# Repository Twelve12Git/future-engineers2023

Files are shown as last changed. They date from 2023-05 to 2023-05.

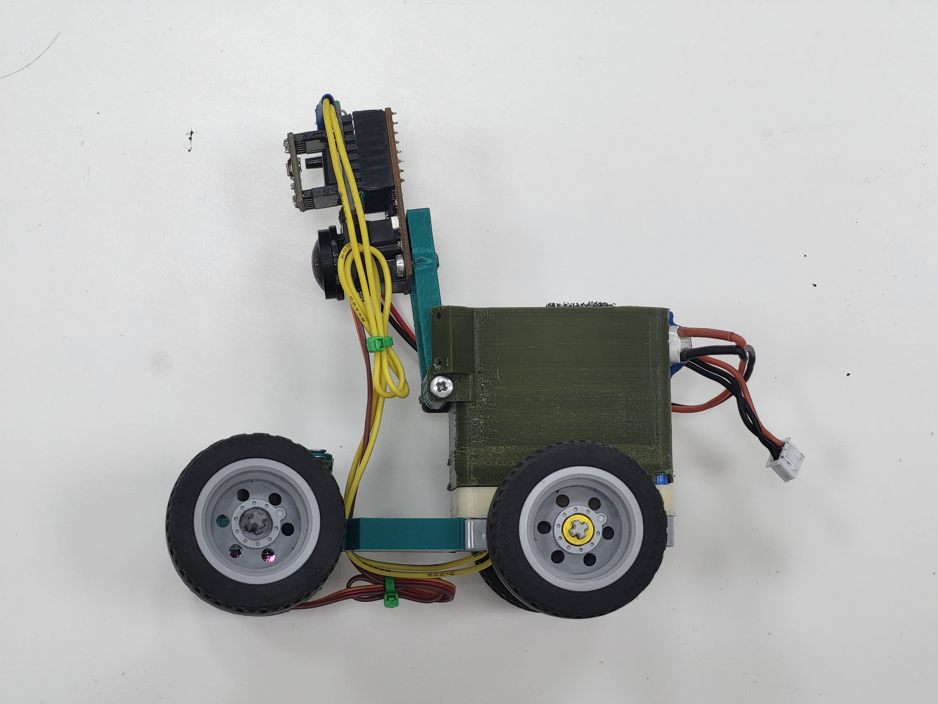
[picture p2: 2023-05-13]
v-photos/слева.jpg

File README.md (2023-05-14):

Во время реализации системы перемещения или же робота, в приоритет ставилась в первую очередь простота сборки и взаимозаменяемость деталей в случае поломки или необходимости внести коррективы в конструкцию. Во время первичного обсуждения конструкции было принято решение использовать О-образную деталь LEGO как основу корпуса, из этого последовало логичное предложение разбить робот на модули, напечатанных на 3д принтере, соединяющихся с  помощью стандартных штифтов вокруг этой детали. Среди таких модулей можно выделить колесную базу состоящую из рулевого и приводного, и камеру модели OpenMV Cam M7, которая также является микроконтроллером. Для управлением колесной базой мы использовали сервопривод и уже привычный нам по опыту предыдущих соревнований драйвер для моторов постоянного тока drv8833, производства компании pololu. Вся сопутствующая электроника (кнопка "пуск", выключатель питания и т.д.) организована в плату навесным монтажом, и крепится над микроконтроллером по аналогии системы шилдов arduino. В качестве элемента питания был выбран литий-полимерный аккумулятор, как самый оптимальный по соотношению размер/производительность. Модели для печати на 3д принтере были смоделированы в программе fusion 360.

Программное обеспечение было разработано под платформу  OpenMV Cam M7 компании  OpenMV. В качестве языка программирования использовался python, как наиболее оптимальный для анализа видео, точнее его версию для микропроцессоров - micropython (https://github.com/micropython/micropython). Алгоритм, используемый нами, представляет собой простую машину состояний, определяющей полосу движения в зависимости от знака и направления движения. За непосредственное управление роботом отвечает ПИД-регулятор, опирающийся на границы поля для позиционировании робота в пространстве. За процессом разработки можно проследить по комментариям к версиям нашего репозитория гит-хаба (https://github.com/Twelve12Git/future-engineers2023).

# описание платы

Все компоненты размещены на макетной плате 30 на 25 мм, драйвер двигателей съемный. Для отладки используется кнопка, запуск робота обеспечивается небольшим тумблером на плате. От кнопки к земле подведен подтягивающий резистор на 10 Ом. Разъемами на плате выполнены в виде гребёнок типа “папа”. Компоненты спаяны одножильным монтажным проводом

# инструкция по сборке

Сначала вам нужно напечатать все недостающие детали, они расположены в папке “Models“

Далее нужно докупить электронные компоненты: OpenMV Cam M7, drv8833, производства компании pololu, кнопка "пуск", выключатель питания, аккумулятор gens acc 450 mah 2s, сервопривод mg90-s, провода 28 awg, двигатель с редуктором 1:100; 

и некоторые части корпуса: lego дифференциал, рама 5x7-модульная серая, lego “гвозди”, lego колеса диаметром 30 мм, винты м3 на 7 мм, Ось с головкой 4-модульная темно-серая, саморезы.

необходимо спаять компоненты на макетной плате, разместив гребенки типа “папа” для последующего соединения с платой камеры.
собрать корпус по приложенной схеме

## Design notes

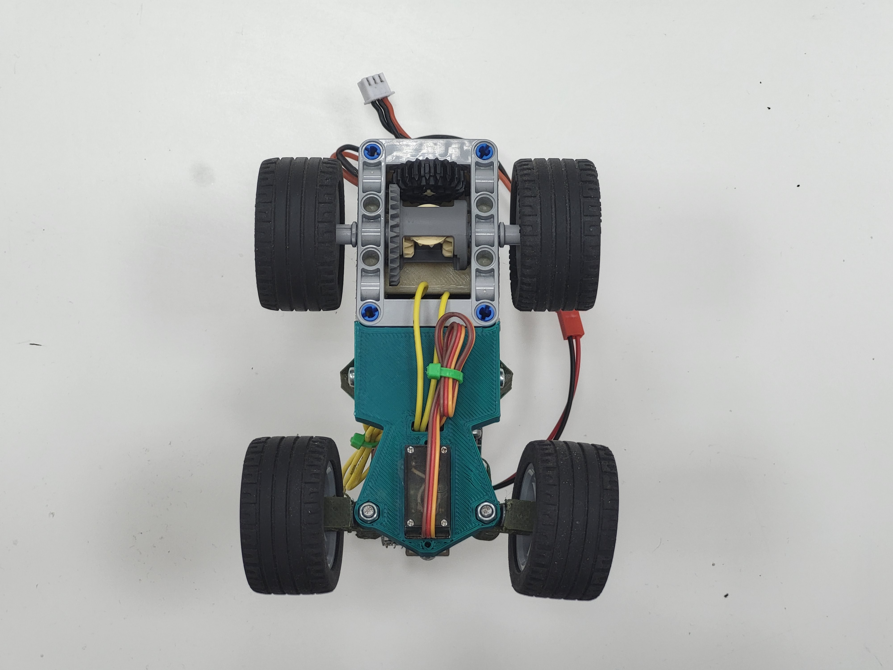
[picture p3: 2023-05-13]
v-photos/снизу.jpg

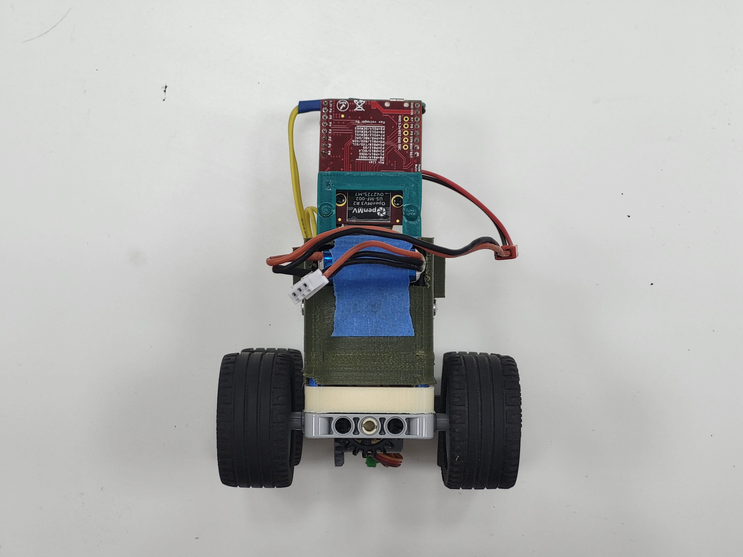
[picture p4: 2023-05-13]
v-photos/сзади.jpg

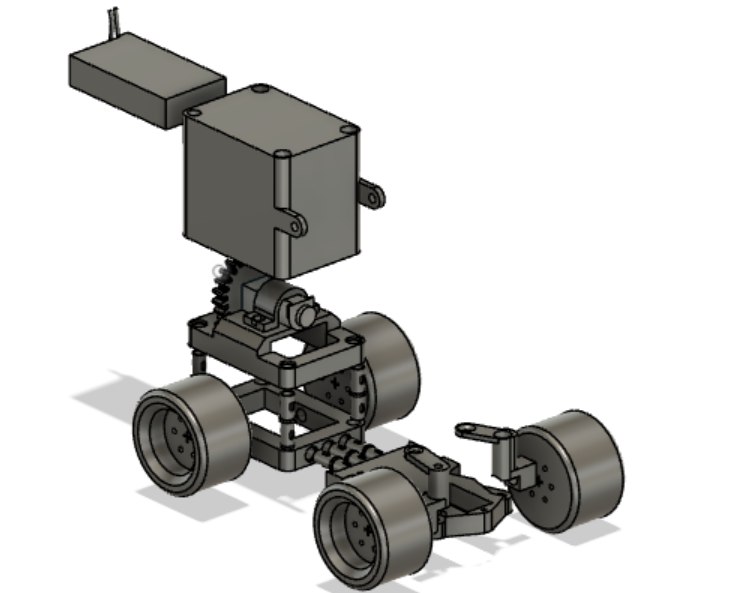
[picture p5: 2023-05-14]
other/Схема сборки.jpg

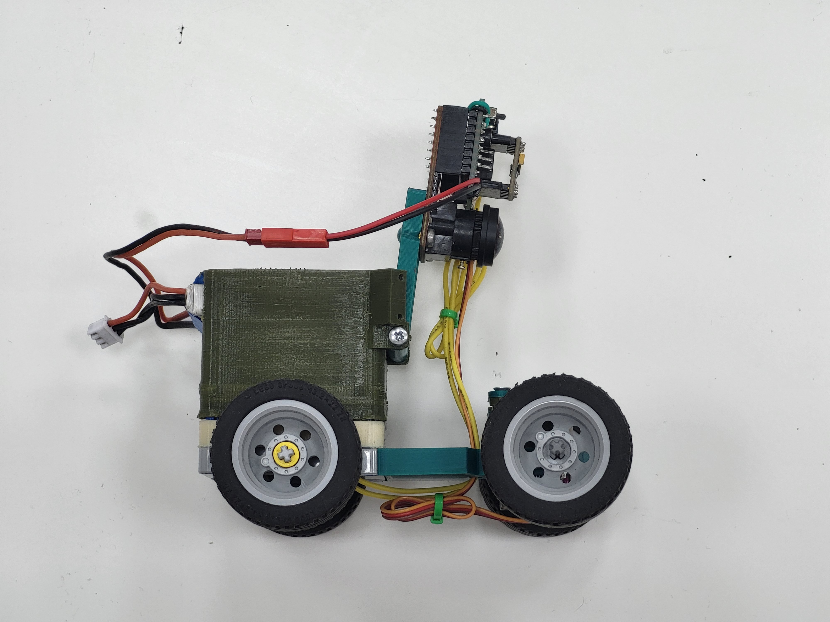
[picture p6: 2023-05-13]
v-photos/справа.jpg

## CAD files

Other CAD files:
models/крепление двигателя.f3d
models/крепление камеры и аккумултора.f3d
models/основание.f3d
models/поворотный механизм тяга 1.f3d
models/поворотный механизм тяга 2.f3d
models/шестерня двигателя.f3d

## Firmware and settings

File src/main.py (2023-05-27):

import sensor, time, pyb
from pyb import Pin, Timer, Servo, LED
from machine import I2C
from vl53l0x import VL53L0X

def constrain(value, min_, max_):
	if min_ <= value and value <= max_: return value
	return min_ if value < min_ else max_

class MyServo:
	def __init__(self, pin):
		self.pin = pin
	def angle(self, angle):
		angle = constrain(angle, -45, 45)
		angle += 90 # уводим из -90 - 90 в 0 - 180
		min_pos = 1000
		max_pos = 2000
		self.pin.pulse_width(min_pos + int((max_pos-min_pos)*(180/angle if angle else 1)))

class Driver:
	"""
	get PWM timer IN out ports (ex Timer(4, freq=1000).channel(3, Timer.PWM, pin=Pin("P9")))
	OpenMV Cam M4 allowed PWM timers: TIM2, TIM3, TIM4
	Timer Pinout:
	Timer 1 Channel 3 Negative -> P0 (PB15)
	Timer 1 Channel 2 Negative -> P1 (PB14)
	Timer 1 Channel 1 Negative -> P2 (PB13)
	Timer 2 Channel 3 Positive -> P4 (PB10)
	Timer 2 Channel 4 Positive -> P5 (PB11)
	Timer 2 Channel 1 Positive -> P6 (PA5)
	Timer 4 Channel 1 Negative -> P7 (PD12)
	Timer 4 Channel 2 Negative -> P8 (PD13)
	Timer 4 Channel 3 Positive -> P9 (PD14) (OpenMV Cam M7/H7 Only - Not OpenMV Cam H7 Plus)
	"""

	def __init__(self, outA1, outA2):
		self.outA1 = outA1
		self.outA2 = outA2

	def set_motor(self, speed):  # -100 <= speed <= 100
		if speed > 0:
			self.outA1.pulse_width_percent(100)
			self.outA2.pulse_width_percent(100-speed)
		else:
			speed = abs(speed)
			self.outA1.pulse_width_percent(100-speed)
			self.outA2.pulse_width_percent(100)

class PID:
	_err_sum = 0
	_prev_err = 0
	u = 0
	def __init__(self, p, i, d, min_es = -100, max_es = 100):
		self._p = p
		self._i = i
		self._d = d
		self._min_err_sum = min_es
		self._max_err_sum = max_es

	def __call__(self, err):
		self._err_sum += constrain(err * self._i, self._min_err_sum, self._max_err_sum)
		self.u = self._p*err + self._err_sum + self._d*(err-self._prev_err)
		self._prev_err = err
		return self.u

	def reset(self):
		self.u = 0
		self._prev_err = 0
		self._err_sum = 0

def atr(roi): # area to roi
	field = ROI_FIELD
	return (field[0]+roi[0], field[1]+roi[1], roi[2], roi[3])

def deb_blobs(img, prnt=True, **blobs):

	for key, value in blobs.items():
		if value and len(value) and None not in value:
			if prnt: print(f"{key}: {*[(x.cx(), x.pixels()) for x in value]}; ", end="\t")
			[img.draw_rectangle(x.rect(), (255, 255, 255)) for x in value]
	if prnt: print("")

def deb(img, **kwargs):
	if kwargs:
		for key, value in kwargs.items():
			print(f"{key}: {value};  ", end="")
		print("")

def deb_roi():
	#img.draw_rectangle(ROI_FIELD, (255, 0, 0)) # поле
	img.draw_rectangle(atr(AREA_WALL_FRONT), (255, 255, 0)) # зона поиска передней стены
	img.draw_rectangle(atr(AREA_WALL_LEFT), (255, 200, 0)) # зона поиска левой стены
	img.draw_rectangle(atr(AREA_WALL_RIGHT), (200, 255, 0)) # зона поиска правой стены
	img.draw_rectangle(atr(AREA_CUBES), (0, 0, 255)) # зона поиска кубиков
	#img.draw_rectangle(atr(AREA_TURNS), (255, 0, 255))
	#img.draw_rectangle(atr(AREA_RED_CUBES), (255, 0, 0)) # зона поиска кубиков
	#img.draw_rectangle(atr(AREA_GREEN_CUBES), (0, 255, 0)) # зона поиска кубиков

pwm_timer = Timer(4, freq=50)
driver = Driver(
	pwm_timer.channel(3, Timer.PWM, pin=Pin("P9")),
	pwm_timer.channel(1, Timer.PWM, pin=Pin("P7"))
)
servo = MyServo(pwm_timer.channel(2, Timer.PWM, pin=Pin("P8")))

main_pid = PID(0.4, 0, 0)

clock = time.clock()

ledr = LED(1)
ledg = LED(2)

xshut = Pin('P3', Pin.OUT_PP, Pin.PULL_NONE)
xshut.value(False)
pyb.delay(500)

i2c = I2C(sda=Pin('P5'), scl=Pin('P4'), freq=400000)

mysensor1=VL53L0X(i2c)
mysensor1.set_address(0x30)

xshut.value(True)
pyb.delay(500)
mysensor2=VL53L0X(i2c)

mysensor2.start()


sensor.reset()
sensor.set_pixformat(sensor.RGB565)
sensor.set_framesize(sensor.QQQVGA) # 80 : 60
sensor.set_vflip(True)
sensor.set_hmirror(True)
sensor.skip_frames(time = 2000)
sensor.set_auto_gain(False)
sensor.set_auto_whitebal(False)
sensor.set_auto_exposure(False, 6000)

GLOBAL_WIDTH = 80
GLOBAL_HIGHT = 60

WIDTH = 80
HIGHT = 40

ROI_FIELD = (0, 25, GLOBAL_WIDTH-0, GLOBAL_HIGHT-25) # x, y, dx, dy
AREA_WALL_FRONT = (35 ,0,WIDTH-35*2 , HIGHT)
AREA_WALL_LEFT = (0, 2, 10, HIGHT-2)
AREA_WALL_RIGHT = (WIDTH-10, 2, 10, HIGHT-2)
AREA_CUBES = (0, 0, WIDTH, int(HIGHT*0.35))
AREA_TURNS = (20, int(HIGHT*0.6), WIDTH-20*2, HIGHT-int(HIGHT*0.6))
AREA_RED_CUBES = (0, 0, int(WIDTH*0.8), int(HIGHT*0.35))
AREA_GREEN_CUBES = (WIDTH-int(WIDTH*0.8), 0, int(WIDTH*0.8), int(HIGHT*0.35))

RED = (0, 100, 14, 127, 8, 127)
GREEN = (0, 100, -128, -15, 12, 127)
BLACK = (0, 46, -128, 127, -128, 19)
ORANGE = (0, 100, -128, 127, 13, 95)
BLUE = (0, 100, -128, 127, -67, -17)

offsets = {
	"red":   30,
	"green": 170,
	None:    250
}

offset = None
prev_cur_cube = None

clockwise = True

cur_millis = 0
force_go_timer = red_timer = 0
in_timer_area_mul = 1
finish_timer = 1500
orange_turn_deadtime = blue_turn_deadtime = 0
blue_turns = orange_turns = turns = 0
left_wall_distance = right_wall_distance = 0

button = Pin("P6", Pin.IN)
while button.value():
	img = sensor.snapshot()
	driver.set_motor(0)
	servo.angle(0)
pyb.delay(600)

############ SPEED ############
driver.set_motor(0)
###############################

while finish_timer >= cur_millis:
	clock.tick()
	img = sensor.snapshot()
	#img = sensor.snapshot().elens_corr(strength = 1.8, zoom = 1.0)

	cur_millis = pyb.millis()
	left_wall_distance = mysensor2.read()
	right_wall_distance = mysensor1.read()
	# ищем блобы
	walls_left = img.find_blobs([BLACK], roi=atr(AREA_WALL_LEFT), pixels_threshold=10)
	walls_right = img.find_blobs([BLACK], roi=atr(AREA_WALL_RIGHT), pixels_threshold=10)
	walls_front = img.find_blobs([BLACK], roi=atr(AREA_WALL_FRONT), pixels_threshold=40)
	red_cubes = img.find_blobs([RED], roi=atr(AREA_CUBES), pixels_threshold=25)
	green_cubes = img.find_blobs([GREEN], roi=atr(AREA_CUBES), pixels_threshold=25)
	turn_orange = img.find_blobs([ORANGE], roi=atr(AREA_TURNS), pixels_threshold=20)
	turn_blue = img.find_blobs([BLUE], roi=atr(AREA_TURNS), pixels_threshold=20)
	# считаем полщади, проверяем что не 0
	red_area   = red_cubes[0].pixels()   if len(red_cubes)   else 0
	green_area = green_cubes[0].pixels() if len(green_cubes) else 0
	left_area  = walls_left[0].pixels()  if len(walls_left)  else 0
	right_area = walls_right[0].pixels() if len(walls_right) else 0
	front_area = walls_front[0].pixels() if len(walls_front) else 0
	# текущий куб (зеленый или красный блоб, в зависимости от площади или None)
	cur_cube = (red_cubes[0] if red_cubes else None) if red_area >= green_area else (green_cubes[0] if green_cubes else None)

	# если потеряли кубик из вида заупскаем таймер
	if cur_cube is None and prev_cur_cube is not None:
		force_go_timer = cur_millis + 1200
	prev_cur_cube = cur_cube
	# считаем повороты
	if len(turn_orange) and orange_turn_deadtime < cur_millis:
		orange_turns += 1
		orange_turn_deadtime = cur_millis + 3000
	if len(turn_blue) and blue_turn_deadtime < cur_millis:
		blue_turns += 1
		blue_turn_deadtime = cur_millis + 3000
	if orange_turns == blue_turns: turns = orange_turns
	# если пересекаем сначала оранжевую линию, то мы едем против часовой стрелика, по дефолту по часовой
	if orange_turns < blue_turns:
		clockwise = False
	# определяем позицию робота относитеьно центра в зависимости от кубика
	if not force_go_timer > cur_millis: # если только что потеряли из виду кубик, то еще секунду не меняем сдвиг относительно центра
		if cur_cube:
			if red_area > green_area:
				offset = "red"
				ledr.toggle()
				ledg.off()
			else:
				offset = "green"
				ledg.toggle()
				ledr.off()
		else:
			offset = None
			ledg.off()
			ledr.off()

	# считаем ошибку
	#offset = "red"
	cur_area     = left_area if     clockwise else right_area
	enother_area = left_area if not clockwise else right_area

	err = offsets[offset] - left_wall_distance


	u = main_pid(err)
	servo.angle(constrain(int(u), -45, 45))

	if turns < 4*3:
		finish_timer = cur_millis + 1000

	deb_roi()
	deb(img, err=err, offset=offset, rwd=right_wall_distance, lwd=left_wall_distance)
	deb_blobs(img, False, current_cube = [cur_cube], lw=walls_left, rw=walls_right, fw=walls_front)
	#deb(img, blue=blue_turns, orng=orange_turns, al=turns)
	#deb_blobs(img,True, bl=turn_blue, orn=turn_orange)

servo.angle(0)
driver.set_motor(0)

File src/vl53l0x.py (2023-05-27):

from micropython import const
import ustruct
import time
import utime
import pyb
import sensor
from pyb import Pin
from machine import I2C

_IO_TIMEOUT = 1000
_SYSRANGE_START = const(0x00)
_EXTSUP_HV = const(0x89)
_MSRC_CONFIG = const(0x60)
_FINAL_RATE_RTN_LIMIT = const(0x44)
_SYSTEM_SEQUENCE = const(0x01)
_SPAD_REF_START = const(0x4f)
_SPAD_ENABLES = const(0xb0)
_REF_EN_START_SELECT = const(0xb6)
_SPAD_NUM_REQUESTED = const(0x4e)
_INTERRUPT_GPIO = const(0x0a)
_INTERRUPT_CLEAR = const(0x0b)
_GPIO_MUX_ACTIVE_HIGH = const(0x84)
_RESULT_INTERRUPT_STATUS = const(0x13)
_RESULT_RANGE_STATUS = const(0x14)
_OSC_CALIBRATE = const(0xf8)
_MEASURE_PERIOD = const(0x04)


class TimeoutError(RuntimeError):
	pass


class VL53L0X:
	def __init__(self, i2c, address=0x29):
		self.i2c = i2c
		self.address = address
		self.init()
		self._started = False

	def _registers(self, register, values=None, struct='B'):
		if values is None:
			size = ustruct.calcsize(struct)
			data = self.i2c.readfrom_mem(self.address, register, size)
			values = ustruct.unpack(struct, data)
			return values
		data = ustruct.pack(struct, *values)
		self.i2c.writeto_mem(self.address, register, data)

	def _register(self, register, value=None, struct='B'):
		if value is None:
			return self._registers(register, struct=struct)[0]
		self._registers(register, (value,), struct=struct)

	def _flag(self, register=0x00, bit=0, value=None):
		data = self._register(register)
		mask = 1 << bit
		if value is None:
			return bool(data & mask)
		elif value:
			data |= mask
		else:
			data &= ~mask
		self._register(register, data)

	def _config(self, *config):
		for register, value in config:
			self._register(register, value)

	def init(self, power2v8=True):
		self._flag(_EXTSUP_HV, 0, power2v8)

		# I2C standard mode
		self._config(
			(0x88, 0x00),

			(0x80, 0x01),
			(0xff, 0x01),
			(0x00, 0x00),
		)
		self._stop_variable = self._register(0x91)
		self._config(
			(0x00, 0x01),
			(0xff, 0x00),
			(0x80, 0x00),
		)

		# disable signal_rate_msrc and signal_rate_pre_range limit checks
		self._flag(_MSRC_CONFIG, 1, True)
		self._flag(_MSRC_CONFIG, 4, True)

		# rate_limit = 0.25
		self._register(_FINAL_RATE_RTN_LIMIT, int(0.25 * (1 << 7)),
					   struct='>H')

		self._register(_SYSTEM_SEQUENCE, 0xff)

		spad_count, is_aperture = self._spad_info()
		spad_map = bytearray(self._registers(_SPAD_ENABLES, struct='6B'))

		# set reference spads
		self._config(
			(0xff, 0x01),
			(_SPAD_REF_START, 0x00),
			(_SPAD_NUM_REQUESTED, 0x2c),
			(0xff, 0x00),
			(_REF_EN_START_SELECT, 0xb4),
		)

		spads_enabled = 0
		for i in range(48):
			if i < 12 and is_aperture or spads_enabled >= spad_count:
				spad_map[i // 8] &= ~(1 << (i >> 2))
			elif spad_map[i // 8] & (1 << (i >> 2)):
				spads_enabled += 1

		self._registers(_SPAD_ENABLES, spad_map, struct='6B')

		self._config(
			(0xff, 0x01),
			(0x00, 0x00),

			(0xff, 0x00),
			(0x09, 0x00),
			(0x10, 0x00),
			(0x11, 0x00),

			(0x24, 0x01),
			(0x25, 0xFF),
			(0x75, 0x00),

			(0xFF, 0x01),
			(0x4E, 0x2C),
			(0x48, 0x00),
			(0x30, 0x20),

			(0xFF, 0x00),
			(0x30, 0x09),
			(0x54, 0x00),
			(0x31, 0x04),
			(0x32, 0x03),
			(0x40, 0x83),
			(0x46, 0x25),
			(0x60, 0x00),
			(0x27, 0x00),
			(0x50, 0x06),
			(0x51, 0x00),
			(0x52, 0x96),
			(0x56, 0x08),
			(0x57, 0x30),
			(0x61, 0x00),
			(0x62, 0x00),
			(0x64, 0x00),
			(0x65, 0x00),
			(0x66, 0xA0),

			(0xFF, 0x01),
			(0x22, 0x32),
			(0x47, 0x14),
			(0x49, 0xFF),
			(0x4A, 0x00),

			(0xFF, 0x00),
			(0x7A, 0x0A),
			(0x7B, 0x00),
			(0x78, 0x21),

			(0xFF, 0x01),
			(0x23, 0x34),
			(0x42, 0x00),
			(0x44, 0xFF),
			(0x45, 0x26),
			(0x46, 0x05),
			(0x40, 0x40),
			(0x0E, 0x06),
			(0x20, 0x1A),
			(0x43, 0x40),

			(0xFF, 0x00),
			(0x34, 0x03),
			(0x35, 0x44),

			(0xFF, 0x01),
			(0x31, 0x04),
			(0x4B, 0x09),
			(0x4C, 0x05),
			(0x4D, 0x04),

			(0xFF, 0x00),
			(0x44, 0x00),
			(0x45, 0x20),
			(0x47, 0x08),
			(0x48, 0x28),
			(0x67, 0x00),
			(0x70, 0x04),
			(0x71, 0x01),
			(0x72, 0xFE),
			(0x76, 0x00),
			(0x77, 0x00),

			(0xFF, 0x01),
			(0x0D, 0x01),

			(0xFF, 0x00),
			(0x80, 0x01),
			(0x01, 0xF8),

			(0xFF, 0x01),
			(0x8E, 0x01),
			(0x00, 0x01),
			(0xFF, 0x00),
			(0x80, 0x00),
		)

		self._register(_INTERRUPT_GPIO, 0x04)
		self._flag(_GPIO_MUX_ACTIVE_HIGH, 4, False)
		self._register(_INTERRUPT_CLEAR, 0x01)

		# XXX Need to implement this.
		#budget = self._timing_budget()
		#self._register(_SYSTEM_SEQUENCE, 0xe8)
		#self._timing_budget(budget)

		self._register(_SYSTEM_SEQUENCE, 0x01)
		self._calibrate(0x40)
		self._register(_SYSTEM_SEQUENCE, 0x02)
		self._calibrate(0x00)

		self._register(_SYSTEM_SEQUENCE, 0xe8)

	def _spad_info(self):
		self._config(
			(0x80, 0x01),
			(0xff, 0x01),
			(0x00, 0x00),

			(0xff, 0x06),
		)
		self._flag(0x83, 3, True)
		self._config(
			(0xff, 0x07),
			(0x81, 0x01),

			(0x80, 0x01),

			(0x94, 0x6b),
			(0x83, 0x00),
		)
		for timeout in range(_IO_TIMEOUT):
			if self._register(0x83):
				break
			utime.sleep_ms(1)
		else:
			raise TimeoutError()
		self._config(
			(0x83, 0x01),
		)
		value = self._register(0x92)
		self._config(
			(0x81, 0x00),
			(0xff, 0x06),
		)
		self._flag(0x83, 3, False)
		self._config(
			(0xff, 0x01),
			(0x00, 0x01),

			(0xff, 0x00),
			(0x80, 0x00),
		)
		count = value & 0x7f
		is_aperture = bool(value & 0b10000000)
		return count, is_aperture

	def _calibrate(self, vhv_init_byte):
		self._register(_SYSRANGE_START, 0x01 | vhv_init_byte)
		for timeout in range(_IO_TIMEOUT):
			if self._register(_RESULT_INTERRUPT_STATUS) & 0x07:
				break
			utime.sleep_ms(1)
		else:
			raise TimeoutError()
		self._register(_INTERRUPT_CLEAR, 0x01)
		self._register(_SYSRANGE_START, 0x00)

	def start(self, period=0):
		self._config(
		  (0x80, 0x01),
		  (0xFF, 0x01),
		  (0x00, 0x00),
		  (0x91, self._stop_variable),
		  (0x00, 0x01),
		  (0xFF, 0x00),
		  (0x80, 0x00),
		)
		if period:
			oscilator = self._register(_OSC_CALIBRATE, struct='>H')
			if oscilator:
				period *= oscilator
			self._register(_MEASURE_PERIOD, period, struct='>H')
			self._register(_SYSRANGE_START, 0x04)
		else:
			self._register(_SYSRANGE_START, 0x02)
		self._started = True

	def stop(self):
		self._register(_SYSRANGE_START, 0x01)
		self._config(
		  (0xFF, 0x01),
		  (0x00, 0x00),
		  (0x91, self._stop_variable),
		  (0x00, 0x01),
		  (0xFF, 0x00),
		)
		self._started = False

	def set_address(self, address):
		self._register(0x8A, address)
		#self.i2c.writeto_mem(self.address, 0x8A, bytes(address))
		self.address = address
		pass
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

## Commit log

2023-05-01 Регламент, первая версия прграммы
2023-05-11 Пид по стенкам, + ошибка кубиков(не работает)
2023-05-11 Пид по одной стенке(по часовой) объезед кубиков работает
2023-05-12 Объезд по часовой почти работает
2023-05-12 Работает по часовой стрелке
2023-05-12 Подчет поворотов
2023-05-13 Подсчет поворотов в основной пограмме
2023-05-13 Работает
2023-05-13 Фото робота
2023-05-14 На случай если все сломаю
2023-05-14 Документация
    [крепление двигателя.f3d, крепление камеры и аккумултора.f3d, основание.f3d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]
2023-05-27 Distance sensors support
